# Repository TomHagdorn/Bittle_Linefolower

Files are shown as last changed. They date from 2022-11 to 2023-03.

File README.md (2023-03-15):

# Robot Dog Bittle - Linefollower
This is a linefollower for the robot dog Bittle. It is based on the [ESP32-CAM](https://www.espressif.com/en/products/hardware/esp32-cam/overview) and uses a linefollower program to detect the line. The ESP32-CAM is connected to the [Bittle](https://www.petoi.com/products/petoi-bittle-robot-dog). 
The bittle is controlled via serial communication. The serial communication is done via the [ESP32-CAM](https://www.espressif.com/en/products/hardware/esp32-cam/overview) and the [Bittle](https://www.petoi.com/products/petoi-bittle-robot-dog).
The linefollower is written in C++. The code is written for the ESP32-CAM.

I will add a slightly more detailed description later.

## Hardware
- [ESP32-CAM](https://www.espressif.com/en/products/hardware/esp32-cam/overview)
- [Bittle](https://www.petoi.com/products/petoi-bittle-robot-dog)

## Software
- [Arduino IDE](https://www.arduino.cc/en/software)
- [OpenCV](https://opencv.org/)
- [Visual Studio Code](https://code.visualstudio.com/)
- [Arduino Extension](https://marketplace.visualstudio.com/items?itemName=vsciot-vscode.vscode-arduino)
- [NodeRed](https://nodered.org/)

## Dependencies for serial communication with node-red
<details>
<summary>Install dependencies on Linux</summary>
<br>
Install Node-Red

Check if Node.js and npm are installed
```
node -v && npm -v
```

If not installed, install Node.js and npm
```
$ sudo apt-get install nodejs && sudo apt-get install npm
```

Install Node-Red
```
$ sudo npm install -g --unsafe-perm node-red
```

Install Node-Red Dashboard
```
$ cd ~/.node-red
$ npm install node-red-dashboard
```

Install Node-Red Node for Bittle
```
$ cd ~/.node-red
$ npm install node-red-contrib-bittle
```

Install Node-Red Serialport
```
$ cd ~/.node-red
$ npm install node-red-node-serialport
```

</details>

<details>
<summary>Install dependencies on Windows</summary>
<br>
Check if Node.js and npm are installed
```
node -v && npm -v
```

If not installed, install Node.js and npm on Windows
```
https://nodejs.org/en/download/
```

Install Node-Red Windows
```	
$ npm install -g --unsafe-perm node-red
```
Install Node-Red Dashboard
```
$ cd %userprofile%\.node-red
$ npm install node-red-dashboard
```

Install Node-Red Node for Bittle
```
$ cd %userprofile%\.node-red
$ npm install node-red-contrib-bittle
```

Install Node-Red Serialport
```
$ cd %userprofile%\.node-red
$ npm install node-red-node-serialport
```

</details>

## Installation
1. [Install the Arduino IDE](https://support.arduino.cc/hc/en-us/articles/360019833020-Download-and-install-Arduino-IDE)
2. [Install the Arduino Extension for Visual Studio Code]
3. Clone this repository
4. Open the folder in Arduino IDE
5. Install the ESP32-CAM Board in the Arduino IDE
6. Go to the nodeRed_variables.h file and change the WIFI ssid and password to your WIFI ssid and password
7. Install the following libraries in the Arduino IDE
    - ArduinoJson
    - WiFi
    - HTTPClient
    - ESPCamera
8. Connect the ESP32-CAM to the computer
9. Select the correct port in the Arduino IDE
10. Select the correct board in the Arduino IDE
    - Board: "AI Thinker ESP32-CAM"
    - Upload Speed: "115200"
    - CPU Frequency: "240MHz (WiFi/BT)"
11. Upload the code to the ESP32-CAM
12. Conect the 3D printed parts to the Bittle
    - Connect the Ultrasonic Sensor Holder to the Camera Holder
    - Connect the Camera Holder to the Bittle
    -Clip the LED-Strip to the Bittle front rail
12. Conect the ESP32-CAM to the Bittle 
    (Caution to not connect the pins wrong to not damage the Bittle or overwirte the firmware)
    - Connect the GND pin of the ESP32-CAM to the GND pin of the Bittle
    - Connect the TX pin of the ESP32-CAM to the RX pin of the Bittle
    - Connect the RX pin of the ESP32-CAM to the TX pin of the Bittle
    - Connect the 5V pin of the ESP32-CAM to the 5V pin of the Bittle
13. Conect the LED-Strip to the ESP32-CAM
    - Connect the GND pin of the ESP32-CAM to the GND pin of the LED-Strip
    - Connect the 5V pin of the ESP32-CAM to the 5V pin of the LED-Strip
    - Connect the D14 pin of the ESP32-CAM to the D pin of the LED-Strip
15. Connect the Ultrasonic Sensor to the ESP32-CAM
    - Connect the GND pin of the ESP32-CAM to the GND pin of the Ultrasonic Sensor
    - Connect the 5V pin of the ESP32-CAM to the 5V pin of the Ultrasonic Sensor
    - Connect the D12 pin of the ESP32-CAM to the Trig pin of the Ultrasonic Sensor
    - Connect the D13 pin of the ESP32-CAM to the Echo pin of the Ultrasonic Sensor
16. Start Node-Red in the terminal
    ```
    node-red
    ```
17. Open the Node-Red flow in the browser
    ```
    http://localhost:1880/
    ```
18. Import the Node-Red flow
    - Click on the hamburger menu in the top right corner
    - Click on import
    - Click on clipboard
    - Copy the content of the nodeRed_flow.json file
    - Paste the content in the import window
    - Click on import
19. Deploy the Node-Red flow
    - Click on the hamburger menu in the top right corner
    - Click on deploy
20. Start the Bittle
21. Go to the Node-Red Dashboard in the browser
    ```
    http://localhost:1880/ui
    ```
22. Set the desired parameters in the Node-Red Dashboard
23. Calibrate using the image server on the ESP#2 ip address
    ```
    http://ip_address_of_the_esp32-cam:81
    ```
24. Start the linefollower using the Node-Red Dashboard

## [Tutorial](<https://i40.fh-aachen.de//courses/dta/activities/bittle/workspace_setup.html#node-red>)

## Tips and tricks
<details>
<summary>Bittle serial cmds</summary>
<br>

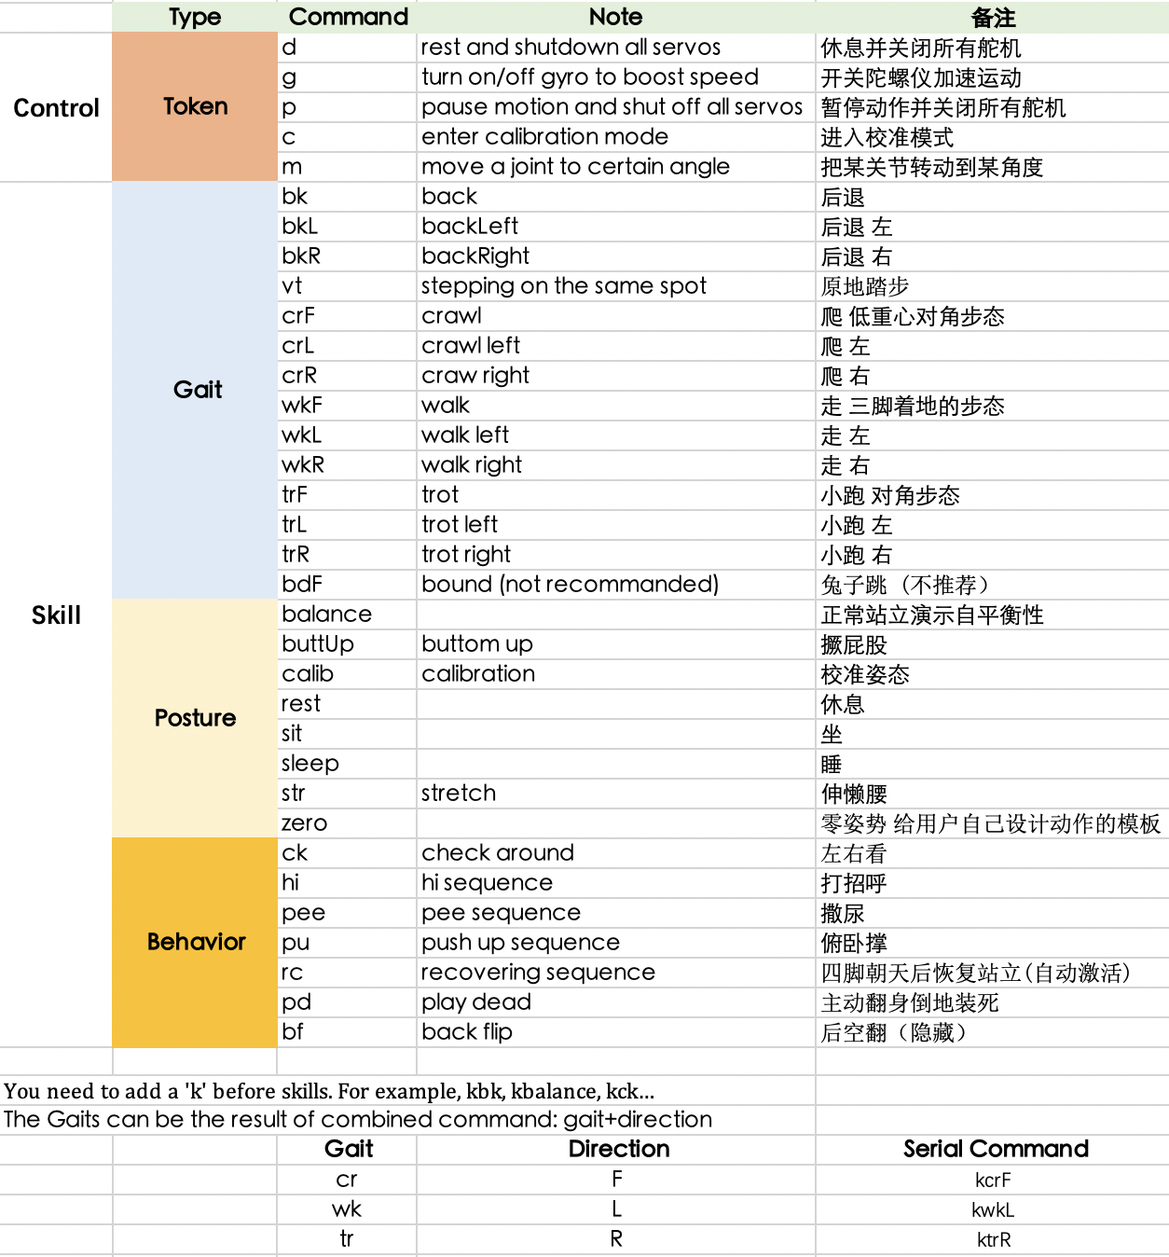
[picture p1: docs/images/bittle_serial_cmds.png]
Getting Started


</details>

## Printed parts
<details>
<summary>Printed parts</summary>
<br>

ESP_Mount.stl

    Mount for the ESP32-CAM. It is printed in PLA+ and it is holding the ESP32-CAM securely in place while the Bittle is moving.
    Alsos it leaves the back open for connection jumper cables.

Mount_Neck_Connection.stl

    Connection between the Camera Holder and the Ultrasonic Sensor Holder. It is printed in PLA+ and it is holding the Camera Holder and the Ultrasonic Sensor Holder securely in place while the Bittle is moving.

UltrasonicSensorHolder.stl
    
        Holder for the Ultrasonic Sensor. It is printed in PLA+ and it is holding the Ultrasonic Sensor securely in place while the Bittle is moving.
        It is screwed to the Camera Holder. With the Mount_Neck_Connection.stl. 

LED_Mount.stl

    Mount for the LED-Strip. It is printed in PLA+ and it is holding the LED-Strip securely in place while the Bittle is moving.
    It is clipped to the Bittle front rail.

standWithCalibration.stl

    Stand for the Bittle. It is printed in PLA+ and it is for testing and calibration without risking the Bittle to fall down.
</details>

## [Official Repository](https://github.com/PetoiCamp)

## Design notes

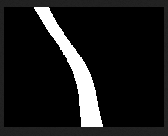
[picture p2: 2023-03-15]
docs/images/Screenshot 2023-03-05 212942.png

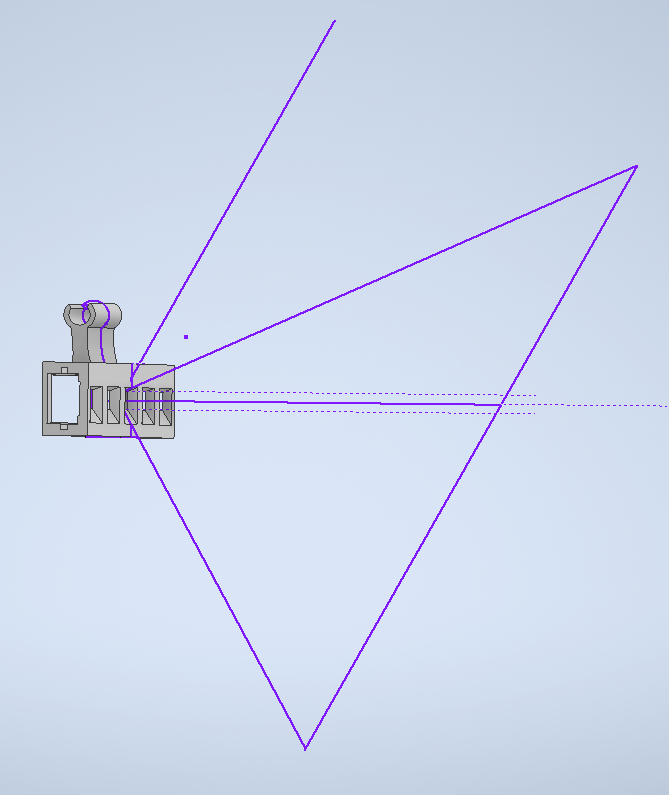
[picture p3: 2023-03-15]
docs/images/Screenshot_20230226_104415.png

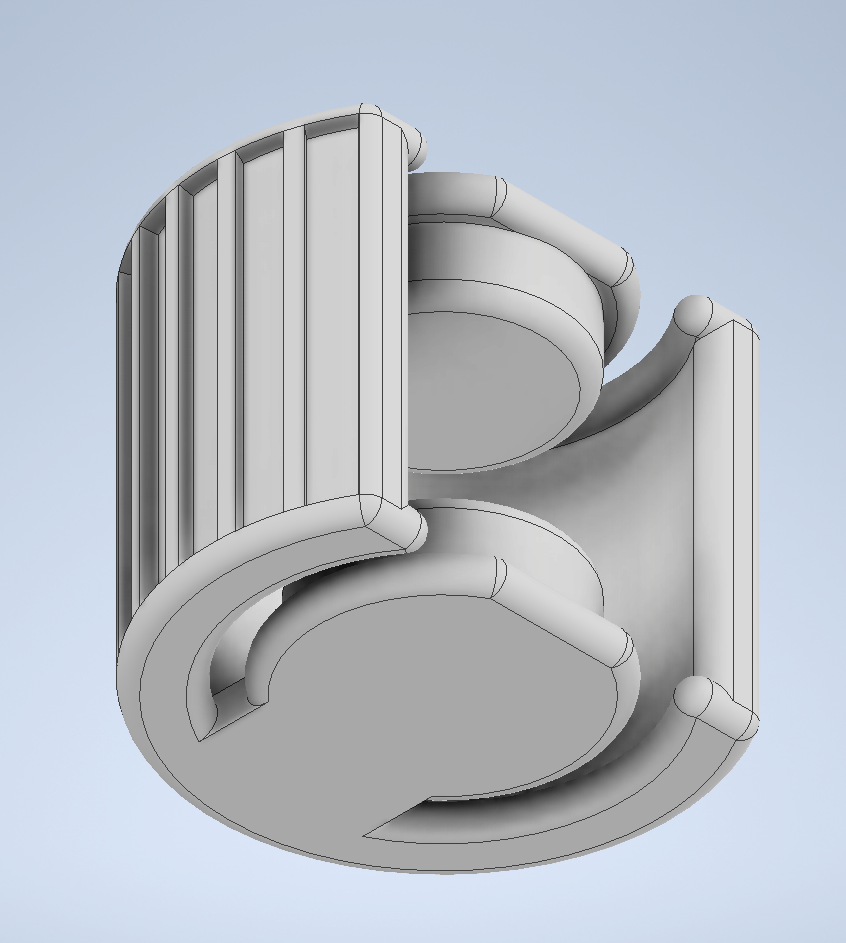
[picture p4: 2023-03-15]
docs/images/Screenshot_20221129_154518.png

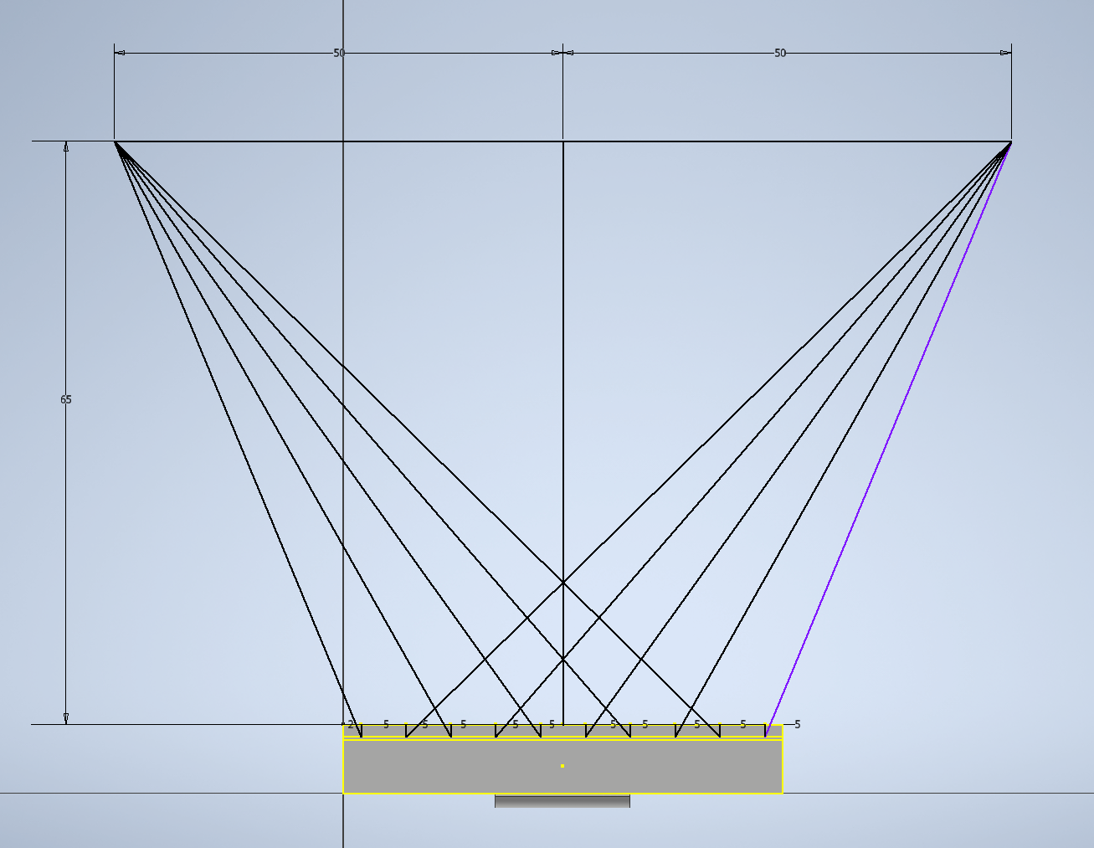
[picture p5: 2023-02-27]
docs/images/Screenshot_20230226_104128.png

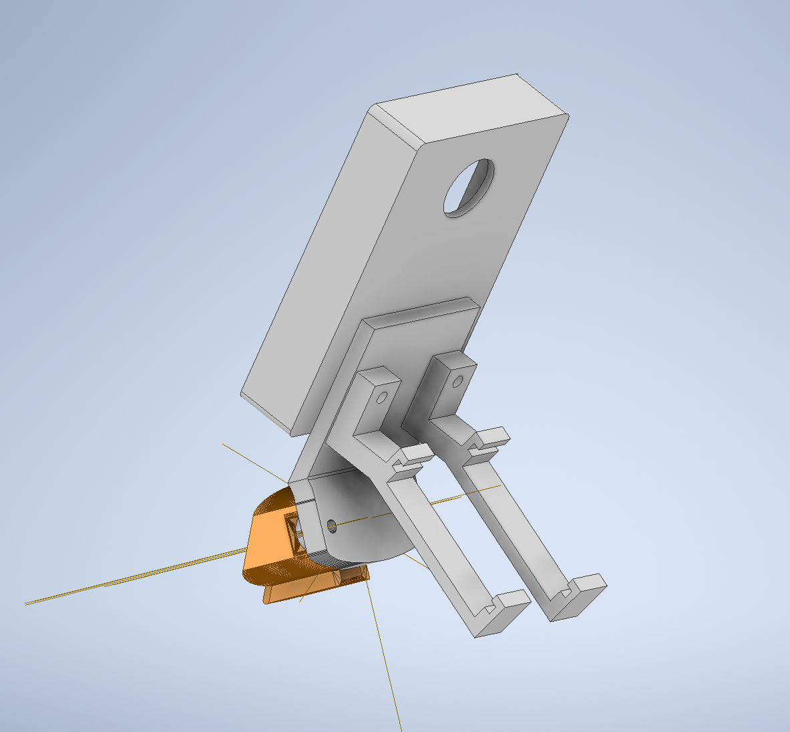
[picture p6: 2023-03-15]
docs/images/Screenshot 2023-03-06 024314.png

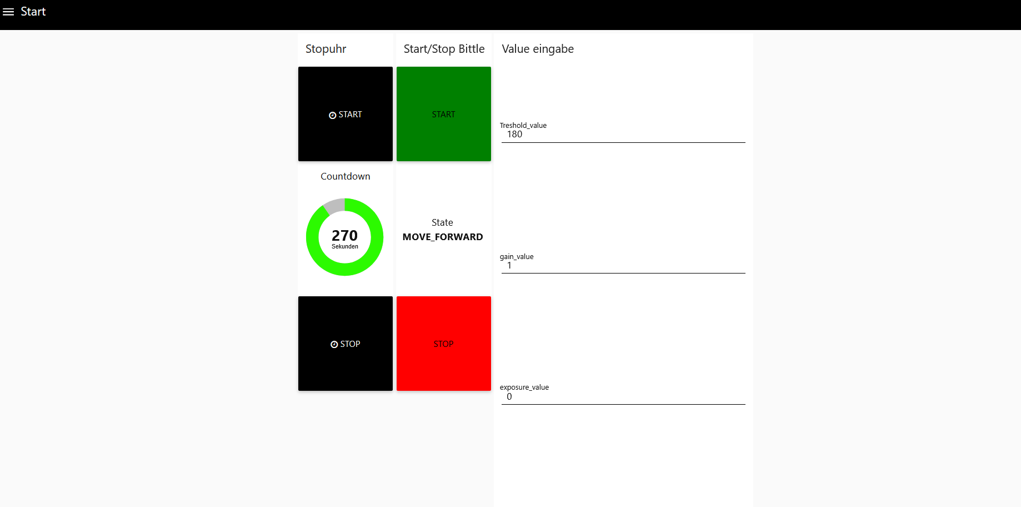
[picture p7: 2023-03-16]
node_red/node_red_dashboard.png

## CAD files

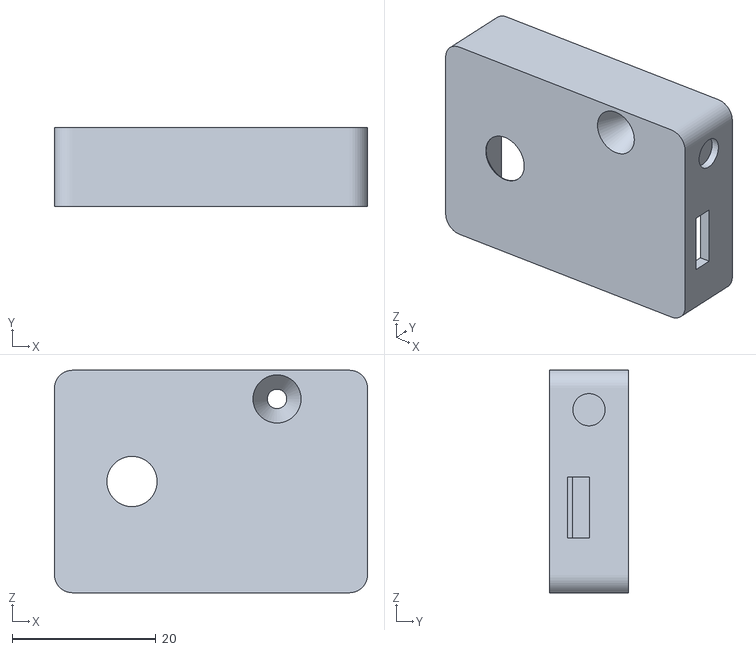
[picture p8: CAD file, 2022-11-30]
docs/STL/Official Bittle/Enclosure.stl
43.6 x 11.0 x 31.0

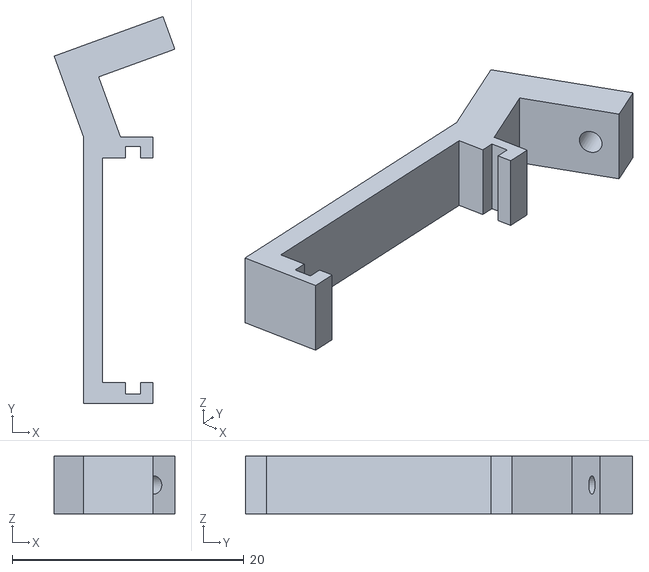
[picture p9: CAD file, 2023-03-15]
docs/STL/UltrasonicSensorHolder.stl
10.4 x 33.4 x 5.00

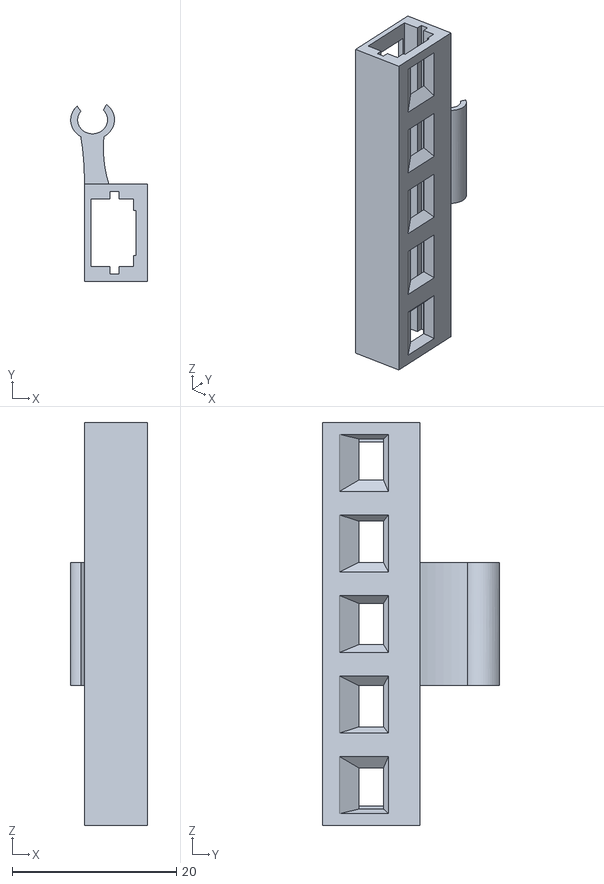
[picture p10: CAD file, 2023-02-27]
docs/STL/LED_Mount.stl
9.33 x 21.5 x 49.0

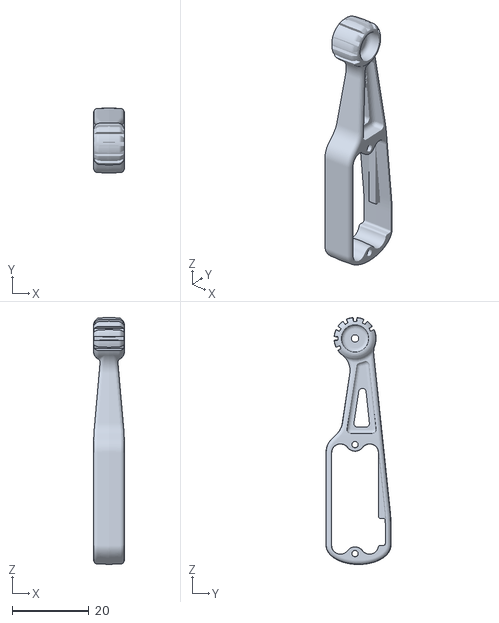
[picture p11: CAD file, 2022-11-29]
docs/STL/Official Bittle/Bittle_shank.stl
8.00 x 17.0 x 64.6

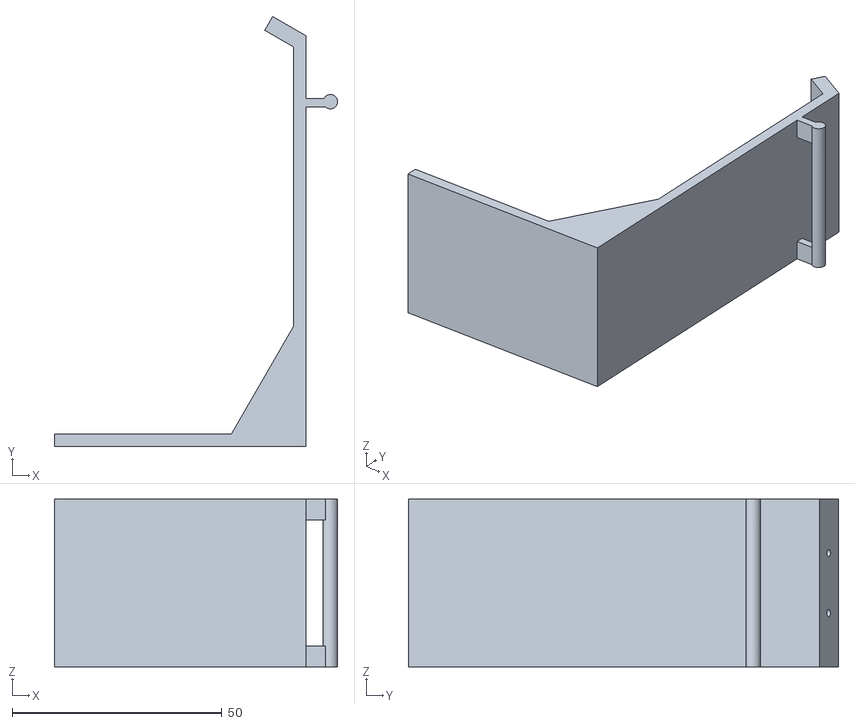
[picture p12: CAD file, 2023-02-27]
docs/STL/ESP32_Test_stand.stl
67.6 x 102.6 x 40.0

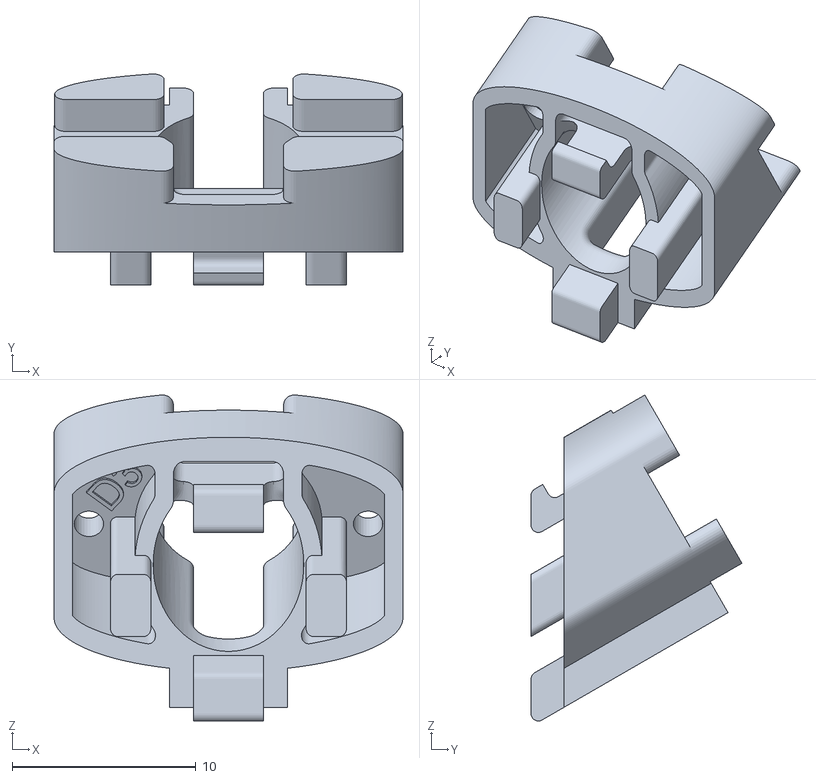
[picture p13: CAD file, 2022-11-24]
docs/STL/Official Bittle/Bittle_neck.stl
19.0 x 11.5 x 17.7

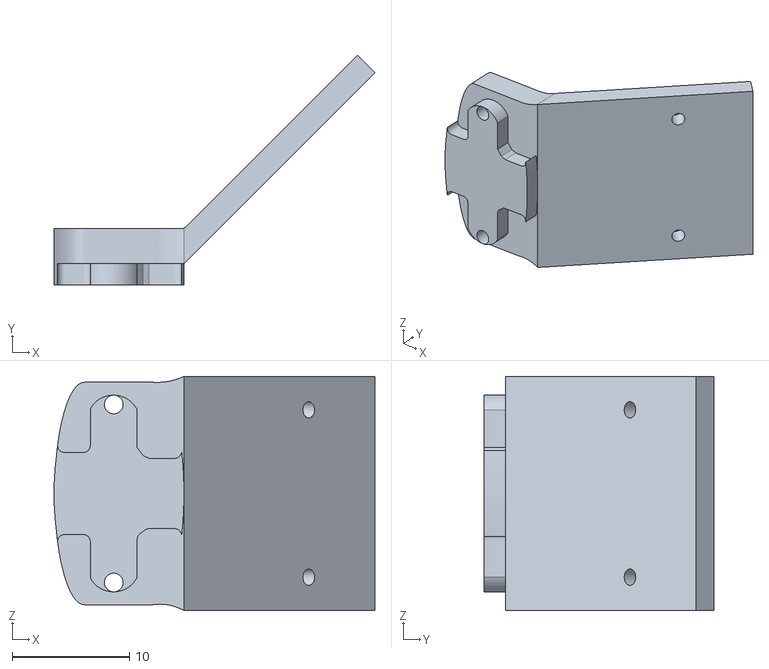
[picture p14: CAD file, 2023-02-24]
docs/STL/Mount_Neck_Connection.stl
27.4 x 19.6 x 20.0

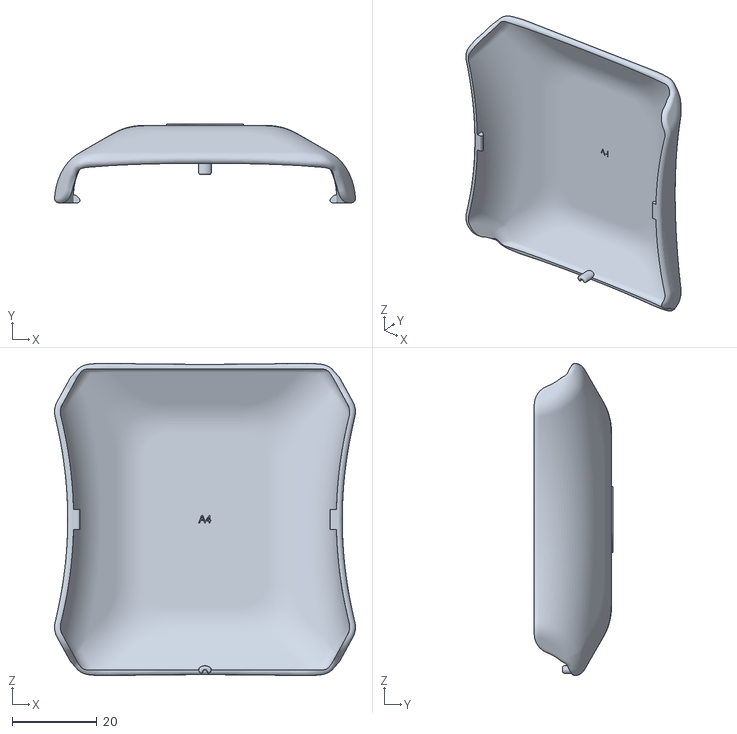
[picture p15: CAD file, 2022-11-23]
docs/STL/Official Bittle/Bittle_Cover.stl
71.2 x 18.6 x 73.9

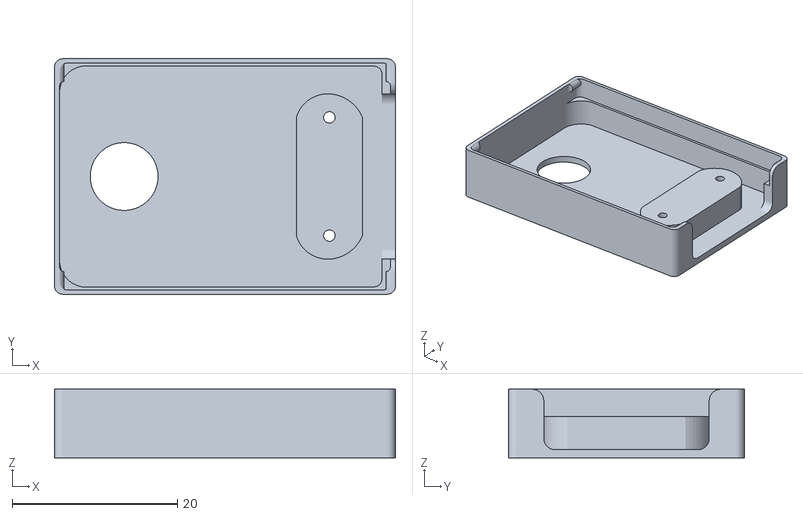
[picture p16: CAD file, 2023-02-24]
docs/STL/ESP32_Mount.stl
41.2 x 28.5 x 8.30

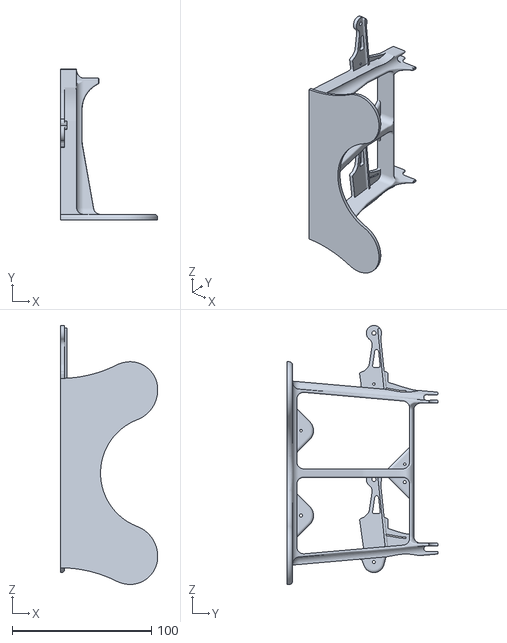
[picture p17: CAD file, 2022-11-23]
docs/STL/Official Bittle/standWithCalibration.stl
70.0 x 108.3 x 186.0

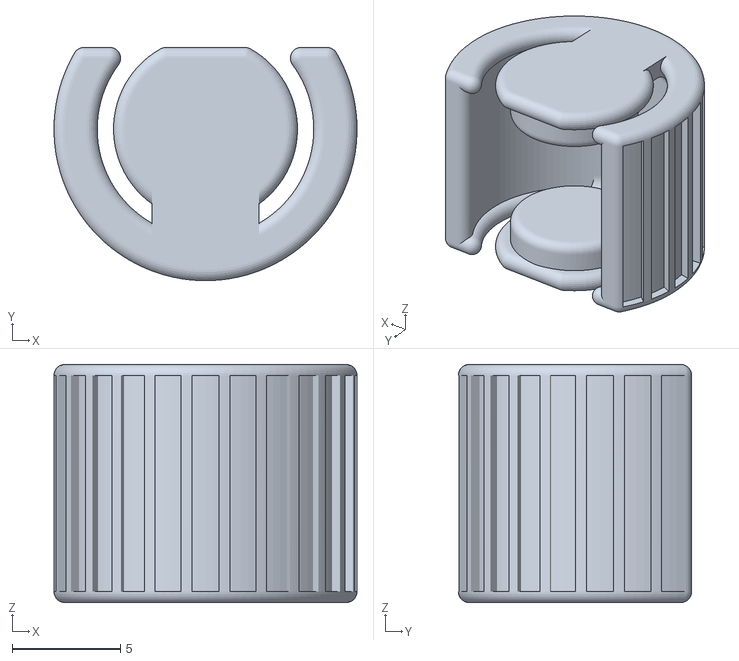
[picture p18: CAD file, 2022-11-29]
docs/STL/Gummifuß.stl
14.0 x 10.8 x 11.0

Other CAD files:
docs/Inventor/ESP_Mount.iam
docs/Inventor/Whole_Mount.iam
docs/Inventor/led-mount.ipt
docs/Inventor/ultrasonic-sensor-direct-mount.ipt

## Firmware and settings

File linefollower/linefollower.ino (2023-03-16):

/**
 * @file linefollower.ino
 * @brief Line follower robot using a camera.
 *
 * This file contains the code for a line follower robot that uses a camera to
 * detect and follow a line. The robot has several behaviors, including
 * following the line, avoiding obstacles, crossing the finish line, and
 * recovering from losing the line.
    \author Tom Hagdorn
*/

/**
    \brief Check for ESP32 board.
*/

#if !defined ESP32
#error Wrong board selected
#endif
#define BAUDRATE 115200

#include "soc/soc.h"          //! Used to disable brownout detection
#include "soc/rtc_cntl_reg.h" //! Used to disable brownout detection

#include <vector>

const int serialSpeed = 115200; ///< Serial data speed to use
// My files
#include "nodeRed_variables.h"
#include "camera_setup.h"
#include "testing.h"
#include "control.h"
#include "light_strip.h"
#include "node_red.h"
#define PIN_S2TX 4

// possible states of the robot
enum State
{
    FOLLOW_LINE,
    AVOID_OBSTACLE,
    CROSS_FINISH_LINE,
    FINISH,
    RECOVER_FROM_NO_LINE,
};

State currentState = FOLLOW_LINE;
// bool to decide if the finish line has been crossed already
bool finish_line_crossed = false;
// define the wifi server

unsigned long lastServerUpdate = 0;
unsigned long startTime = 0;
unsigned long obstacleTime = 7000;



/**
 * Initializes various components used in the device.
 * Initializes serial communication, disables brownout detector, initializes the camera,
 * sets up the on-board flash, sets LED brightness, and sets up the ultrasound sensor.
 * Additionally, it sets the modes of the trigPin and echoPin.
 *
 * @return None.
 */
void setup()
{
    Serial.begin(serialSpeed); ///< Initialize serial communication
    BittleSerial.begin(BAUDRATE ,SERIAL_8N1, PIN_S2TX);
    WRITE_PERI_REG(RTC_CNTL_BROWN_OUT_REG, 0); ///< Disable 'brownout detector'

    // Serial.print(("\nInitialising camera: "));
    if (initialiseCamera())
    {
        // Serial.println("OK");
    }
    else
    {
        // Serial.println("Error!");
    }
    setup.wifi();
    setupOnBoardFlash();
    setLedBrightness(ledBrightness);
    server.on("/Start", HandleClienttrue);
    server.on("/Stop", HandleClientfalse);
    // Wifi functions to start or stop the update()
    server.on("/status", handle_status);
 
    send_image();
    Update_node_red_value();


    // Ultrasound sensor setup
    strip_setup();

    pinMode(trigPin, OUTPUT); // Sets the trigPin as an Output
    pinMode(echoPin, INPUT);  // Sets the echoPin as an Input
}
/**
 * The main loop of the program.
 *
 * Performs image processing on the camera capture every 320 milliseconds, including applying
 * a Gaussian blur, thresholding, and updating the device's state accordingly. Also updates
 * the server every 900 milliseconds (commented out). Prints the loop time to the serial monitor.
 *
 * @return None.
 */
void loop()
{

    //cycle_led_strip();

    if (millis() - lastCamera > 320)
    {
        // unsigned long loopTimeStart = millis();
        esp_err_t res = camera_capture();

        if (res == ESP_OK)
        {
            gaussianBlur(kernelSize);
            // sobel();
            threshold_image();
            unsigned long thresholdTime = millis();
            //  Serial.print("Threshold time: ");
            //  Serial.println(thresholdTime - loopTimeStart);
            update();
            unsigned long updateTime = millis();
            // Serial.print("Update time: ");
            // Serial.println(updateTime - thresholdTime);
            update_movement();
            // unsigned long movementTime = millis();
            //  Serial.print("Movement time: ");
            //  Serial.println(movementTime - updateTime);

            // update server every 600ms to save resources
            // TODO Fix this
            if (millis() - lastServerUpdate >= 900)
            {
                server.handleClient();
                lastServerUpdate = millis();
            }

            // print image to serial monitor
            // capture_still();
            // free the sobel image gradient buffer
            // delete[] gradient;
            lastCamera = millis();
        }
        // unsigned long loopTimeEnd = millis();
        // Serial.print("Loop time: ");
        // Serial.println(loopTimeEnd - loopTimeStart);
        // return the frame buffer back to the driver for reuse
        esp_camera_fb_return(fb);
    }
    // Print the loop timeg
}

/**
 * The `update()` function updates the state of the robot based on the current state.
 * This function is called repeatedly in the `loop()` function.
 * 
 * The robot has several states, including:
 * 
 * - FOLLOW_LINE: the robot follows the line on the ground.
 * - AVOID_OBSTACLE: the robot detects an obstacle and maneuvers around it.
 * - CROSS_FINISH_LINE: the robot crosses the finish line.
 * - RECOVER_FROM_NO_LINE: the robot has lost the line and tries to recover.
 * - FINISH: the robot has finished the course.
 * 
 * Depending on the current state, this function may call other functions to perform specific actions,
 * such as line following, obstacle avoidance, or finish line detection.
 * 
 * This function also sets the current movement state of the robot, which is used to control the
 * motors and move the robot.
 */
void update()
{

    switch (currentState)
    {
    case FOLLOW_LINE:
        if (detect_obstacle() == true && (millis() - obstacleTime >= 5000))
        {
            //Serial.println("\nAVOID_OBSTACLE");
            currentState = AVOID_OBSTACLE;
            lastStateChangeTime = millis();
        }
        else
        {

            if (check_for_horizontal_line() && (millis() - finishTime >= 3000))
            {
                //Serial.println("\nCROSS_FINISH_LINE");
                currentState = CROSS_FINISH_LINE;
                lastStateChangeTime = millis();
            }
            else if (line_follower())
            {
                lastStateChangeTime = millis();
                // line follower returned true, indicating that the line was found
            }
            
            break;
        }
        break;
    case AVOID_OBSTACLE:
        if (avoid_obstacle() == true)
        {
            //Serial.println("\nFOLLOW_LINE");
            currentState = FOLLOW_LINE;
            lastStateChangeTime = millis();
            finishTime = millis();
            obstacleTime = millis();
        }
        else if (millis() - lastStateChangeTime >= 100000)
        {
            // If 10 seconds have passed since last state change, switch back to FOLLOW_LINE
            //Serial.println("\nFOLLOW_LINE (timeout)");
            currentMovementState = STATE_SLEEP;
            // currentState = FOLLOW_LINE;
            lastStateChangeTime = millis();
        }
        break;
        break;
    case CROSS_FINISH_LINE:
        if (crossFinishLine() == true && finish_line_crossed == false)
        {
            finish_line_crossed = true;
            //Serial.println("\nFOLLOW_LINE");
            finishTime = millis();
            currentState = FOLLOW_LINE;
            lastStateChangeTime = millis();
        }
        else if (finish_line_crossed == true)
        {
            //Serial.println("\nFINISH");
            currentState = FINISH;
        }
        break;
    case RECOVER_FROM_NO_LINE:
        static int recoverAttempts = 0;
        if (recover() == true)
        {
            //Serial.println("\nFOLLOW_LINE");
            currentState = FOLLOW_LINE;
            lastStateChangeTime = millis();
            recoverAttempts = 0; // reset recover attempts counter
        }
        else if (recoverAttempts >= 3)
        {
            // If recover attempts exceed 3, switch back to FOLLOW_LINE
            Serial.println("\nFOLLOW_LINE (max recover attempts reached)");

            currentMovementState = STATE_SLEEP;
            lastStateChangeTime = millis();
            recoverAttempts = 0; // reset recover attempts counter
        }
        else
        {
            recoverAttempts++;
        }
        break;
    case FINISH:
        if (lastStateChangeTime > 1500)
        {
            // if this is the first time in the FINISH state, set the last state change time
            currentMovementState = STATE_SLEEP;
        }
        break;
    }
}

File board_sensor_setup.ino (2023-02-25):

#if !defined ESP32
#error Wrong board selected
#endif

#define CAMERA_MODEL_AI_THINKER

#include "esp_camera.h" ///< Header file for camera obtained from https://github.com/espressif/

#include "driver/ledc.h" ///< To enable onboard Illumination/flash LED pin attached on 4

#include "soc/soc.h"          //! Used to disable brownout detection
#include "soc/rtc_cntl_reg.h" //! Used to disable brownout detection

#include <vector>
// Depenencies for image processing

#include <WiFi.h>
#include <WebServer.h>

const char *ssid = "Get off my Lan!";
const char *password = "prettyflyforAWifi";

unsigned long stateTime = 0;

WebServer server(80);

//! Image resolution:
/*!
    default = "const framesize_t FRAME_SIZE_IMAGE = FRAMESIZE_VGA"

    Other available Frame Sizes:
    160x120 (QQVGA), 128x160 (QQVGA2), 176x144 (QCIF), 240x176 (HQVGA),
    320x240 (QVGA), 400x296 (CIF), 640x480 (VGA, default), 800x600 (SVGA),
    1024x768 (XGA), 1280x1024 (SXGA), 1600x1200 (UXGA)
*/

const framesize_t FRAME_SIZE_IMAGE = FRAMESIZE_UXGA; // FRAMESIZE_QQVGA
camera_fb_t *fb;

//! Image Format
/*!
    Other Available formats:
    YUV422, GRAYSCALE, RGB565, JPEG, RGB888
*/

#define PIXFORMAT PIXFORMAT_GRAYSCALE;



#define IMAGE_WIDTH 800  ///< Image size Width
#define IMAGE_HEIGHT 600 ///< Image size Height

//! Camera exposure
/*!
    Range: (0 - 1200)
    If gain and exposure both set to zero then auto adjust is enabled
*/

int cameraImageExposure = 0;

//! Image gain
/*!
    Range: (0 - 30)
    If gain and exposure both set to zero then auto adjust is enabled
*/
int cameraImageGain = 0;

const uint8_t ledPin = 4;                  ///< onboard Illumination/flash LED pin (4)
int ledBrightness = 8;                     ///< Initial brightness (0 - 255)
const int pwmFrequency = 50000;            ///< PWM settings for ESP32
const uint8_t ledChannel = LEDC_CHANNEL_0; ///< Camera timer0
const uint8_t pwmResolution = 8;           ///< resolution (8 = from 0 to 255)

const int serialSpeed = 115200; ///< Serial data speed to use

// minimum line lenth for line detection
const int min_line_length = 10;

//! Camera setting
/*!
    Camera settings for CAMERA_MODEL_AI_THINKER OV2640
    Based on CameraWebServer sample code by ESP32 Arduino

*/
#if defined(CAMERA_MODEL_AI_THINKER)
#define PWDN_GPIO_NUM 32
#define RESET_GPIO_NUM -1
#define XCLK_GPIO_NUM 0
#define SIOD_GPIO_NUM 26
#define SIOC_GPIO_NUM 27
#define Y9_GPIO_NUM 35
#define Y8_GPIO_NUM 34
#define Y7_GPIO_NUM 39
#define Y6_GPIO_NUM 36
#define Y5_GPIO_NUM 21
#define Y4_GPIO_NUM 19
#define Y3_GPIO_NUM 18
#define Y2_GPIO_NUM 5
#define VSYNC_GPIO_NUM 25
#define HREF_GPIO_NUM 23
#define PCLK_GPIO_NUM 22
#endif

uint32_t lastCamera = 0; ///< To store time value for repeated capture

// variables updated by nodered
int pixel_threshold = 55;
int recover_time  = 500;
int Obst_left_t =1;
int Obst_straight_t=1;
int Obst_right_t =1;
int Line_width=1;
int Fin_line_width=1;
int currentlinewidth = 1;
int currentfinlinewidth =1;



//possible states of the robot  **************************************************************
enum State
{
    FOLLOW_LINE,
    AVOID_OBSTACLE,
    CROSS_FINISH_LINE,
    FINISH,
    RECOVER_FROM_NO_LINE,
};

State currentState = FOLLOW_LINE;
// bool to decide if the finish line has been crossed already
bool finish_line_crossed = false;
// define the wifi server

//define state change time
static unsigned long lastStateChangeTime = 0;

// Setup Ultrsonic sensor   ********************************************************************
const int TRIGGER_PIN = 4;
const int ECHO_PIN = 5;


void setup()
{
    Serial.begin(serialSpeed); ///< Initialize serial communication

    WRITE_PERI_REG(RTC_CNTL_BROWN_OUT_REG, 0); ///< Disable 'brownout detector'

    // Serial.print(("\nInitialising camera: "));
    if (initialiseCamera())
    {
        // Serial.println("OK");
    }
    else
    {
        // Serial.println("Error!");
    }

    setupOnBoardFlash();
    setLedBrightness(ledBrightness);
    //Nodered setup
    WiFi.begin(ssid, password);
    int connRes = WiFi.waitForConnectResult();
    if (connRes == WL_CONNECTED) {
        //Serial.print("Connected to WiFi network with IP: ");
        //TODO uncomment this to print the IP address
        //TODO David
        //Serial.println(WiFi.localIP());
        server.begin();
        //Call functions for the variable nodered values
        //Change_Treshold_value();
    } else {
        Serial.println("Connection Failed!");
        esp_restart();
        return;
    }
    

}
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

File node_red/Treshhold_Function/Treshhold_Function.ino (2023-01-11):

#include <WiFi.h>
#include <WebServer.h>


const char* ssid     = "Vodafone-BC8D";
const char* password = "T8hHQQCFQrpLMgGb";
int teshold_Value = 1; // the variable that you want to update

WebServer server(80);

void setup() {
  
  Serial.begin(115200);
  WiFi.begin(ssid, password);
  server.begin();
  Change_Value();
}

void loop() {

  server.handleClient();
  Serial.println(teshold_Value);

}

void Change_Value(){
    server.on("/update-variable", HTTP_GET, []() {
    String newValue = server.arg("value");
    teshold_Value = newValue.toInt();
  });
}

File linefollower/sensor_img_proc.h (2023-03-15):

// Pin definitions for ultrasound sensor
#define trigPin     12
#define echoPin     13



//TODO not enough memory unfortunately figure something out
//int* gradient = new int[fb->height * fb->width];

/**
 * @brief Applies a Gaussian blur to the image buffer.
 * 
 * @param kernelSize The size of the Gaussian kernel to use. This must be an odd integer.
 */
void gaussianBlur(int kernelSize) {
  float kernel[] = { 1, 2, 1, 2, 4, 2, 1, 2, 1 }; // 3x3 Gaussian kernel

  int radius = kernelSize / 2;   

  int height = fb->height;
  int width = fb->width;

  for (int y = 0; y < height; y++) {
    for (int x = 0; x < width; x++) {
      float sum = 0;
      float weight = 0;

      for (int ky = -radius; ky <= radius; ky++) {
        for (int kx = -radius; kx <= radius; kx++) {
          int px = x + kx;
          int py = y + ky;

          if (px >= 0 && px < width && py >= 0 && py < height) {
            float w = kernel[(ky + radius) * kernelSize + (kx + radius)];
            sum += w * fb->buf[py * width + px];
            weight += w;
          }
        }
      }

      fb->buf[y * width + x] = (uint8_t)(sum / weight);
    }
  }
}

/**
 * @brief Thresholds the image buffer to binary (black and white).
 * 
 * @note This function assumes that the frame buffer (`fb`) contains grayscale pixel values.
 * 
 * @param pixel_threshold The threshold value to use. Pixels with values greater than this will be set to 255 (white), 
 *                        while pixels with values less than or equal to this will be set to 0 (black).
 */
void threshold_image()
{
    // get the height and width of the frame
    int height = fb->height;
    int width = fb->width;

    

    // threshold the entire frame
    for (int row = 0; row < height; row++)
    {
        for (int col = 0; col < width; col++)
        {
            int index = row * width + col;

            // threshold the pixel at the current index
            // if the pixel is less than 210, set it to 255 (white)
            fb->buf[index] = (fb->buf[index] > pixel_threshold) ? 255 : 0;
        }
    }
}

/**
 * @brief the middle point of a white line in the specified region of the frame.
 *
 * @return The x-coordinate of the middle point of the white line, or -1 if no valid line is found.
 */
int get_middle_point()
{   
    double start_fraction = 0;
    double end_fraction = 1.0;
    // initialize the starting and ending x-coordinates to zero
    int start_x = 0;
    int end_x = 0;
    // flag to track if we have found the start of the white pixels
    bool found_start = false;
    // variable to track the number of consecutive non-white pixels
    int consecutive_non_white = 0;
    // variable to track the number of consecutive white pixels to check row validity
    int consecutive_white = 0;
    // row counter
    int valid_row_counter = 0;
    // vector to store the middle points of each row
    std::vector<int> middle_points;

    // calculate the start and end rows based on the start and end fractions
    int start_row = fb->height * start_fraction;
    int end_row = fb->height * end_fraction;
    // check if the start and end rows are valid
    if ((end_row > fb->height) || (start_row < 0) || (start_row > end_row))
    {
        // invalid start and end rows, so return -1
        Serial.println("Invalid start and end rows");
        Serial.println("Height: " + String(fb->height) + ", Start Row: " + String(start_row) + ", End Row: " + String(end_row));
        Serial.println("Need 0 <= start_row < end_row <= height");
        return -1;
    }
    // iterate over the rows in the specified range
    for (int y = start_row; y < end_row; y++)
    {
        // iterate over the columns in the current row
        for (int x = 0; x < fb->width; x++)
        {   
    
            // get the current pixel value
            uint8_t pixel = fb->buf[y * fb->width + x];

            // if the pixel is white (i.e., its value is above the threshold)
            if (pixel == 255)
            {
                // if we haven't found the start of the white pixels yet,
                // set the start x-coordinate to the current x-coordinate
                consecutive_white++;
                // reset the consecutive non-white pixels counter
                consecutive_non_white = 0;
                // if we haven't found the start of the white pixels yet,
                if (!found_start)
                {
                    start_x = x;
                    found_start = true;
                }
                // update the ending x-coordinate to the current x-coordinate
                end_x = x;
            }
            else
            {
                // increment the consecutive non-white pixels counter
                consecutive_non_white++;
            }
            // if we have seen 15 consecutive non-white pixels, set the end x-coordinate to
            // the current x-coordinate minus 15
            if (consecutive_non_white >= 8)
            {
                end_x = x - 15;
                consecutive_non_white = 0;
                found_start = false;
            }
            // if we have seen 40 consecutive white pixels, then we have found a valid row
            if (consecutive_white >= 20 && found_start)
            {
                valid_row_counter++;
                // calculate the middle x-coordinate of the white pixels
                int middle_point = (end_x + start_x) / 2;
                // add the middle point to the vector

                middle_points.push_back(middle_point);
            }
        }
    }
    // if we have found at least one valid row
    if (valid_row_counter > line_width)
    {
        // sort the middle points
        std::sort(middle_points.begin(), middle_points.end());
        // calculate the median middle point
        int median_middle_point = middle_points[middle_points.size() / 2];
        // return the median middle point
        return median_middle_point;
    }
    // if we haven't found any valid rows, return -1
    else
    {
        return -1;
    }
}

/**
 * @brief Gets the distance to the nearest object in front of the ultrasonic sensor.
 *  
 * @return The distance to the nearest object in front of the ultrasonic sensor.
*/
int get_distance()
{
    // Clears the trigPin
    digitalWrite(trigPin, LOW);
    delayMicroseconds(2);
    // Sets the trigPin on HIGH state for 10 micro seconds
    digitalWrite(trigPin, HIGH);
    delayMicroseconds(10);
    digitalWrite(trigPin, LOW);
    // Reads the echoPin, returns the sound wave travel time in microseconds
    long duration = pulseIn(echoPin, HIGH);
    // Calculating the distance
    int distance = duration * 0.034 / 2;
    // Prints the distance on the Serial Monitor
    //SSerial.print("Distance: ");
    //Serial.println(distance);
    return distance;
}
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

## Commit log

2022-11-23 added node red flows
2022-11-23 update readme add install and node red flow
2022-11-23 update readme add stl feet
2022-11-23 add png for readme add pcv folder
    [Gummifuß-V2.stl, standWithCalibration.stl]
2022-11-23 add cover stl
    [Bittle_Cover.stl]
2022-11-24 add updated feet and example code for esp-cam linfefollower
    [Bittle_neck.stl, Gummifuß-V3.stl, MuIntelligentCamera_mount.stl]
2022-11-24 Add esp32 cam connection
    [partitions.csv]
2022-11-29 add shank cam feetv5 stl
    [Bittle_shank.stl, ESP32-Cam - Base.stl, ESP32-Cam - Case.stl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]
2022-11-30 add camera-neck stl and the arduino case stl
    [BallNut.STL, CAM-Neck.stl, CAM_holder_V1.stl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]
2022-12-04 add cam neck, tastk on doxygen
    [CAM-Neck_V3.stl]
2022-12-11 add files for linefollower on ESP32 CAM
    [partitions.csv]
2022-12-11 adjusting the image processing
    [partitions.csv]
2022-12-11 Updated image proc and node red flow
2022-12-14 linefollower now works some calibration needs to be done
2022-12-14 red_node timer und start
2022-12-19 solve some merge issues
    [linefollower.ino]
2022-12-19 resolving some merge issues
    [linefollower.ino]
2023-01-08 modified functions to fit statemachine add new states add recovery avoid and some other core functions
    [linefollower.ino]
2023-01-08 state machine has now timer to be not as harsh about losing the line for a second
2023-01-10 everything works exept avoid obstacle
    [linefollower.ino]
2023-01-10 Revert "Merge branch 'master' into TomH_Img_Proc"
    This reverts commit 8da583588f5f85ad8bda00e29fc29ea22caae816, reversing
    changes made to df3fa3cb61efcb5a333b614966f4d5746f028946.
    [linefollower.ino]
2023-01-10 Revert "Revert "Merge branch 'master' into TomH_Img_Proc""
    This reverts commit 040fe2b0fcca2d8d8a94da6bb2e018dec0835c8c.
    [linefollower.ino]
2023-01-10 Revert " everything works exept avoid obstacle"
    This reverts commit 0f3b33a324892c8eba9529398d2b7627d3a69c06.
    [linefollower.ino]
2023-01-11 add node red functions and json
    [defaultConfig.txt]
2023-02-23 cleaned up the folder and split the folder to allow for better workflow
    [partitions.csv]
2023-02-24 Add base for calibration functions, add some stl inventor files
    [BallNut.STL, Bittle_Cover.stl, Bittle_neck.stl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]
2023-02-25 cleaned up again this time its not stupid
    [led-mount_V2.stl]
2023-02-26 add ulrtra sonic sensor obstackle detection
2023-02-26 add ultra sonic sensor obstacle detection
    [TestStand_V1.stl, led-mount_V3.stl, led-mount_v4.stl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]
2023-02-26 split the obstacle detection function to match the sensor and controll split
2023-02-28 fixed pointer issues, get_still not working tho
    [linefollower.ino, sensor_img_proc.h]
2023-02-28 add camera setup
2023-03-01 server works again but no other camera capture can be made then
2023-03-01 updated statemachine to only print each command once and also have programm without while loops
2023-03-01 working figured out sobel problem not enugh memory
    [linefollower.ino, sensor_img_proc.h]
2023-03-03 updated obstacle avoidance and readme
    [sensor_img_proc.h]
2023-03-05 add some pics finctions work now exept cross finish line
    [led-mount_V2.stl, led-mount_V3.stl, ultrasonic-sensor-direct-mount-V2.stl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]
2023-03-06 obstacle avoidance works a bit
    [linefollower.ino]
2023-03-15 add some files
    [Kimpletter ESP Mount Complete.iam, ultrasonic-sensor-direct-mount-V5.stl]
2023-03-15 ome changes
    [ESP32_Mount.stl, ESP32_Test_stand.stl, ESP_Mount.iam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]
